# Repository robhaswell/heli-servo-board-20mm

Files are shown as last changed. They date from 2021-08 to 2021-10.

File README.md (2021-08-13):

# Helicopter servo bus board
This project is a PCB designed to facilitate wiring a helicopter servo bus to a drone flight controller.

Mounting pattern: 20x20mm.

This bus supports 3 servo outputs and so must be used for helicopters with a motor-driven tail connected to an ESC.

The connector footprints are for 1.25mm pitch connectors, such as Molex PicoBlade or JST 1.25.

**Please read the [assembly instructions](#assembly-instructions) before ordering or use**

PCB render with connectors
PCB render without connectors

## Instructions for ordering

First: Read the [assembly instructions](#assembly-instructions) and determine that this board is suitable for your setup.

You can order this PCB with a prototyping service.
Below are instructions for using [JLCPCB](https://jlcpcb.com):

1. Visit https://jlcpcb.com/.
2. Click "Order now' from the menu - do not use the quoting box.
3. Upload the file [gerber.zip](gerber.zip).
4. You may use the default options, but I suggest selecting a thickness of 0.8mm or 1.0mm. I also prefer the black PCBs.
5. Add to basket and check out. Take care to review the shipping options. FedEx is good if you would like this sooner, but there is usually a very cheap option depending on your location.

## Assembly instructions

To assemble you will need:

1. PicoBlade or JST 1.25 connectors to match your servo plugs.
2. JST-XH 2-way horizontal connector `S2B-XH-A(LF)(SN)`  
or  
JST-XH vertical or other 2.54mm connector.  
or  
JST-PH or other 2.00mm connector.

**Pay very close attention to plug wiring, pins and polarities!!!**

There are no standard servo plug pinouts.
Test everything with a multimeter before soldering, and again before powering on.

1. Make sure that your intended servos have the control wire as pin 1 or 3.
2. Solder your servo input connector, or use the solder pads directly. These are the control lines from your PWM servo outputs on your FC. If using solder pads you can solder directly to the wire pads, connector pads, or both. Use silicone glue to secure the wire.
3. Solder your servo connectors so that the control wire is the topmost pin, the row labelled "1".
4. Check the position of your servo positive and negative wires. They should line up with "V" (positive) and "G" (negative). If they do not (e.g. Blade servos) then you will need to install the power connector backwards.
5. Check the pins of your power connector and verify correct pins with a multimeter, then solder.
6. Test all connections a final time.

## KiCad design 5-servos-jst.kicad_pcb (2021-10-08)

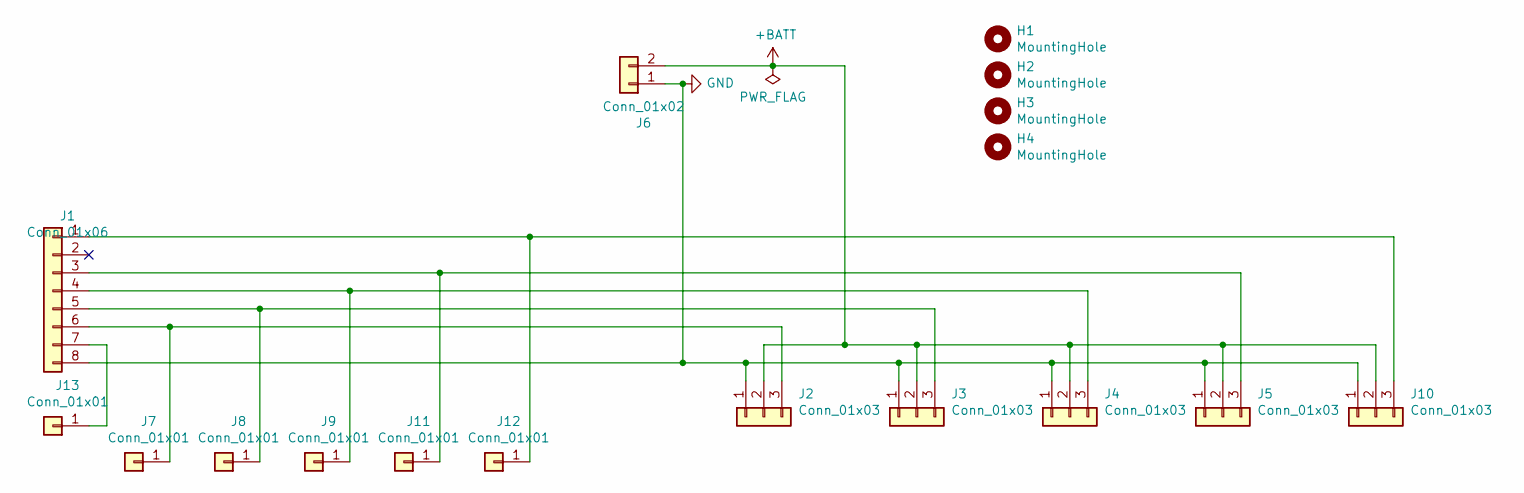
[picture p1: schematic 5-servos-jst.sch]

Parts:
H1, H2, H3, H4: MountingHole; MountingHole_3.2mm_M3
J1: Conn_01x06; JST_SHL_SM08B-SHLS-TF_1x08-1MP_P1.00mm_Horizontal
J2, J3: Conn_01x03; PinHeader_1x03_P2.54mm_Vertical
J4, J5, J10: Conn_01x03; Molex_PicoBlade_53047-0310_1x03_P1.25mm_Vertical
J6: Conn_01x02; JST_XH_S2B-XH-A_1x02_P2.50mm_Horizontal
J7, J8, J9, J11, J12, J13: Conn_01x01; SolderWirePad_1x01_SMD_1x2mm

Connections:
+BATT: J2.2, J3.2, J4.2, J5.2, J6.2, J10.2
GND: J1.8, J2.1, J3.1, J4.1, J5.1, J6.1, J10.1
unnamed: J1.1, J10.3, J12.1
unnamed: J1.3, J5.3, J11.1
unnamed: J1.4, J4.3, J9.1
unnamed: J1.5, J3.3, J8.1
unnamed: J1.6, J2.3, J7.1
unnamed: J1.7, J13.1

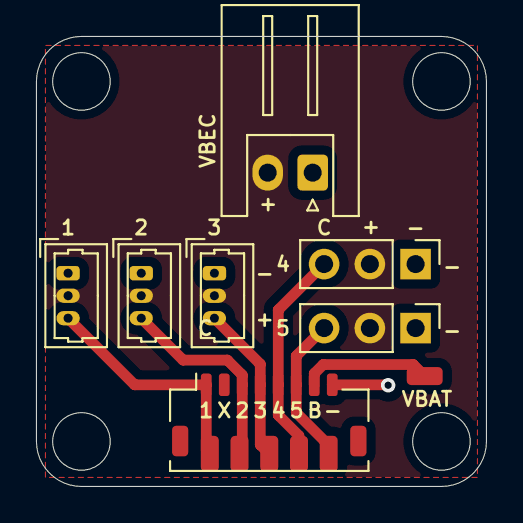
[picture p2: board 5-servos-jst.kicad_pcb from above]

Board: 2 copper layers, 25.0 x 25.0 mm, 17 parts (0 on the bottom side), 8 nets.

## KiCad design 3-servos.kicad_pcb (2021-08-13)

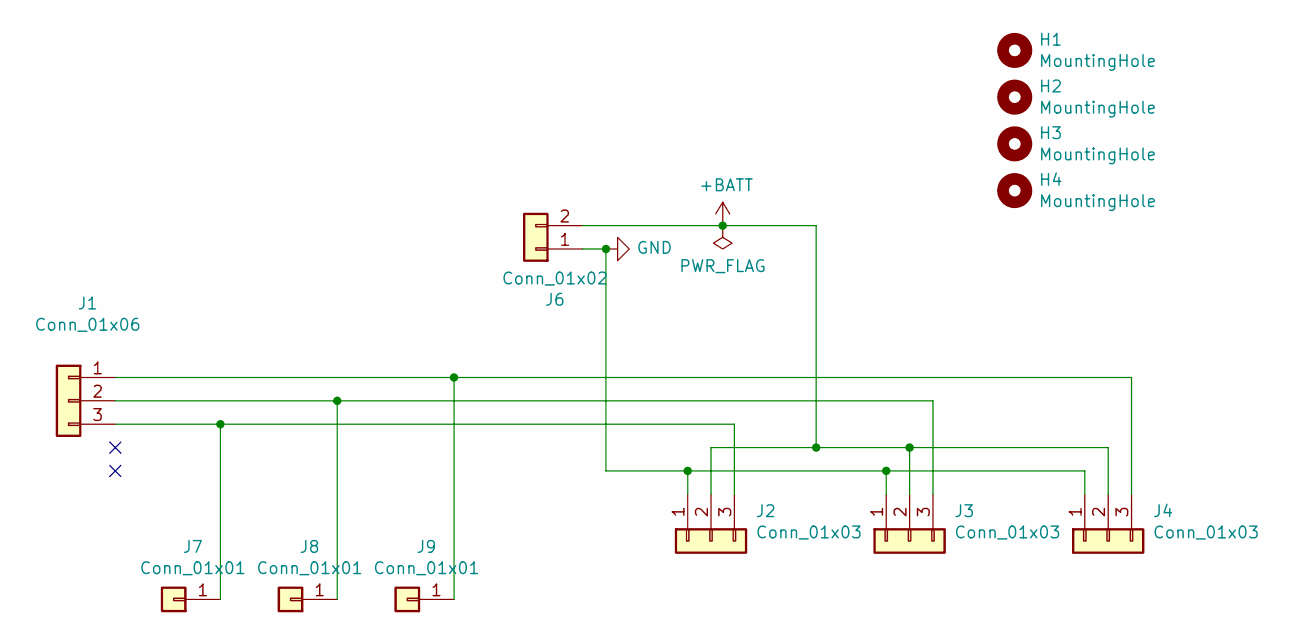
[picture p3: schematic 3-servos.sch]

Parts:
H1, H2, H3, H4: MountingHole; MountingHole_2.2mm_M2
J1: Conn_01x06; Molex_PicoBlade_53047-0310_1x03_P1.25mm_Vertical
J2, J3, J4: Conn_01x03; Molex_PicoBlade_53047-0310_1x03_P1.25mm_Vertical
J6: Conn_01x02; JST_XH_S2B-XH-A_1x02_P2.50mm_Horizontal
J7, J8, J9: Conn_01x01; SolderWirePad_1x01_SMD_1x2mm

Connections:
+BATT: J2.2, J3.2, J4.2, J6.2
GND: J2.1, J3.1, J4.1, J6.1
unnamed: J1.1, J4.3, J9.1
unnamed: J1.2, J3.3, J8.1
unnamed: J1.3, J2.3, J7.1

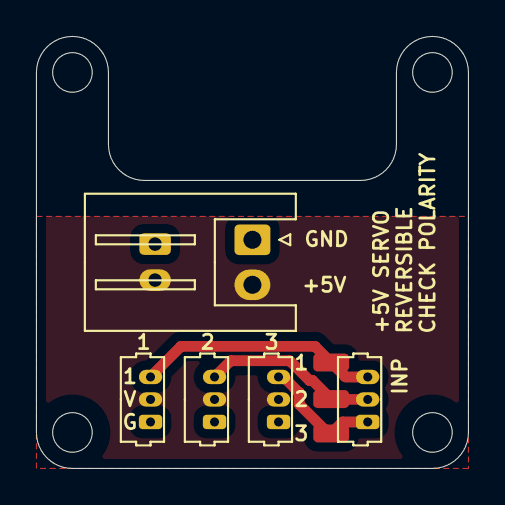
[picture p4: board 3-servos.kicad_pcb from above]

Board: 2 copper layers, 24.0 x 24.0 mm, 12 parts (0 on the bottom side), 5 nets.

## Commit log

2021-08-13 Create 5-servo version.
    [3-servos-B_Cu.gbr, 3-servos-B_Mask.gbr, 3-servos-B_Paste.gbr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]
2021-10-08 Add 5 servo board with JST and M3 holes.
    [5-servos-jst-B_Cu.gbr, 5-servos-jst-B_Mask.gbr, 5-servos-jst-B_Paste.gbr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]
